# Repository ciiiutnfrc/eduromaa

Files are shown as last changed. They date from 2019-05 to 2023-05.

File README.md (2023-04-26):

# EduRoMAA - Robot Educativo Abierto y de Bajo Costo

El robot móvil EduRoMAA fue desarrollado con fines didácticos para la enseñanza de programación de sistemas embebidos utilizando la EduCIAA (versión educativa de la [Computadora Industrial Abierta Argentina](http://www.proyecto-ciaa.com.ar/)) en el [Centro de Investigación en Informática para la Ingeniería](http://ciii.frc.utn.edu.ar/PublicacionesCIII) de la [Universidad Tecnológica Nacional, Facultad Regional Córdoba](https://www.frc.utn.edu.ar/), bajo el proyecto [Robot móvil de hardware y software abierto con fines educativos en ingeniería electrónica](https://ciii.frc.utn.edu.ar/ciii/proyecto-utn4884/).

El robot EduRoMAA es un robot de tracción diferencial fabricado mediante corte láser e impresión 3D.
Dispone de dos ruedas de tracción controladas de forma independiente a fin de generar la trayectoria deseada, y una semiesfera que hace de apoyo.
Cuenta también con sensores de bajo costo comunes en robótica tales como: paragolpes, tacómetro en las ruedas, sensor de distancia por ultrasonido y sensores infrarrojos para la detección de línea; además de comunicación inalámbrica utilizando el protocolo Bluetooth.
El robot incluye las baterías de alimentación, el cargador por microUSB y fuente de tensión regulada.

El EduRoMAA cuenta con:
  * Tacómetros en las ruedas para la medición de velocidad.
  * Sensor de distancia por ultrasonido en la parte frontal.
  * Sensores de detección de líneas en la parte inferior.
  * Paragolpes en la parte trasera para detección de colisiones.
  * Comunicación inalámbrica por Bluetooth.
  * Bocina o buzzer.
  * Llave de encendido/apagado con LED indicador.
  * Baterías incorporadas con indicador de nivel y cargador por micro-USB.

Para la realización del EduRoMAA se utilizó únicamente software libre: [KiCAD](https://www.kicad.org/) para el circuito electrónico y PCB, [FreeCAD](https://www.freecadweb.org/) para la estructura mecánica y Eclipse IDE con GCC-ARM para el firmware.

## Videos

  * Despiece 3D de los componentes del EduRoMAA: [https://www.youtube.com/watch?v=gHjaK3ePBkI](https://www.youtube.com/watch?v=gHjaK3ePBkI).
  * Prueba de tracción del EduRoMAA: [https://www.youtube.com/watch?v=mks88KmrYdc](https://www.youtube.com/watch?v=mks88KmrYdc).

## Publicaciones
  * Gonzalo Perez-Paina, Martín Baudino, Diego Gonzalez-Dondo, Facundo Navarro, and Patricio Reus Merlo. **"Robot móvil de diseño abierto y bajo costo con fines didácticos basado en la educiaa"**. _In Proceedings of the X Jornadas Argentinas de Robótica (JAR)_. Neuquén, Argentina, 2019.

## Más información
  * [Características principales](doc/Caracteristicas.md).
  * Construcción:
    - Estructura mecánica.
    - Placa de acondicionamiento.
  * Ensamblado.
  * [Conexión con EduCIAA](doc/ConexionEduCIAA.md).
  * [Conexión con BluePill](doc/PlacaAdaptacionBluePill.md).
  * [Códigos de prueba para la versión EduCIAA](codigo/EduCIAA/)
  * [Códigos de prueba para la versión BluePill](codigo/BluePill/)

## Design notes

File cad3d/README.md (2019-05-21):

# Diseño en FreeCAD para corte láser

Archivos del diseño del robot utilizando [FreeCAD](https://www.freecadweb.org/). 
Se incluyen los archivos para realizar el corte láser en MDF (Medium Density Fibreboard) de 3mm de espesor.

## Los archivos son:

* EduRoMAATapas: diseño de la tapa inferior y superior.

* EduRoMAALaterales: diseño de los laterales izquierdo y derecho. 

* EduRoMAAFrente: diseño del frente donde se coloca el sensor de distancia por ultrasonido.

* EduRoMAAAtras: diseño de la parte trasera donde se sujeta el módulo Bluethoot

## Contenido de directorios

* **extra**: 
  * DibujoPCB: archivo de dibujo del contorno de la parte inferior del robot (exportado de FreeCAD para el diseño del PCB en KiCAD)
  * EsambleEstructura: archivo FreeCAD con el ensamble de la estructura del robot
* **pdf**: archivo pdf para el corte láser
* **svg**: archivos exportados desde FreeCAD para el corte láser

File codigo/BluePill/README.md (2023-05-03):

# Ejemplos de código en Arduino para la BluePill

En este directorio se ecuentran distintos ejemplos de código Arduino para testear los diferentes périfericos del EduRoMAA.

### Periféricos GPIOS: 
 * [Placa Adaptadora](testeoPlacaAdaptadora/testeoPlacaAdaptadora.ino): LEDs y Pulsadores de la placa
 * [Bocina](testeoBocina/testeoBocina.ino) 
 * [Paragolpes](testeoParagolpes/testeoParagolpes.ino)
 * [Sonar](testeoSonar/testeoSonar.ino)

### PWM
 * [Motores](testeoMotoresPWM/testeoMotoresPWM.ino) 

### Entrdas ADC:

* [Sensor seguidor de linea](testeoInfraRojo/testeoInfraRojo.ino)

### Entradas Timer

* [Encoder de las ruedas](testeoEncoders/testeoEncoders.ino)

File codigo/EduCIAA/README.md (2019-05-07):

* Buzzer: 
	- [x] Asignación de pines 
	- [x] Creación de header y source
	- [x] Codificación de módulo
	- [x] Implementación de test
	- [x] Test OK 

* Motores
	- [x] Asignación de pines 
	- [x] Creación de header y source
	- [x] Codificación de módulo
	- [x] Implementación de test
	- [ ] Test OK: Driver no funciona a 3.3V 

* Líneas Infrarrojos
	- [x] Asignación de pines 
	- [x] Creación de header y source
	- [x] Codificación de módulo
	- [x] Implementación de test
	- [ ] Test OK : Vref del ADC es 3.3 y señales salen con 0-5V

* Paragolpes
	- [x] Asignación de pines 
	- [x] Creación de header y source
	- [x] Codificación de módulo
	- [x] Implementación de test
	- [x] Test OK 

* Sonar
	- [x] Asignación de pines 
	- [x] Creación de header y source
	- [x] Codificación de módulo
	- [x] Implementación de test
	- [x] Test OK 

* Encoders IR
	- [x] Asignación de pines 
	- [x] Creación de header y source
	- [x] Codificación de módulo
	- [x] Implementación de test
	- [x] Test OK 

* Bluetooth
	- [x] Asignación de pines 
	- [ ] Creación de header y source
	- [ ] Codificación de módulo
	- [ ] Implementación de test
	- [ ] Test OK 
 
- [ ] 
- [ ] 
- [ ] 
- [ ] 
- [ ] 
- [ ]

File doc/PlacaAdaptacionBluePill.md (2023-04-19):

# Placa de adaptación para BluePill

Es un placa para adaptar el conexionado del EduRoMAA con la placa de desarrollo BluePill.

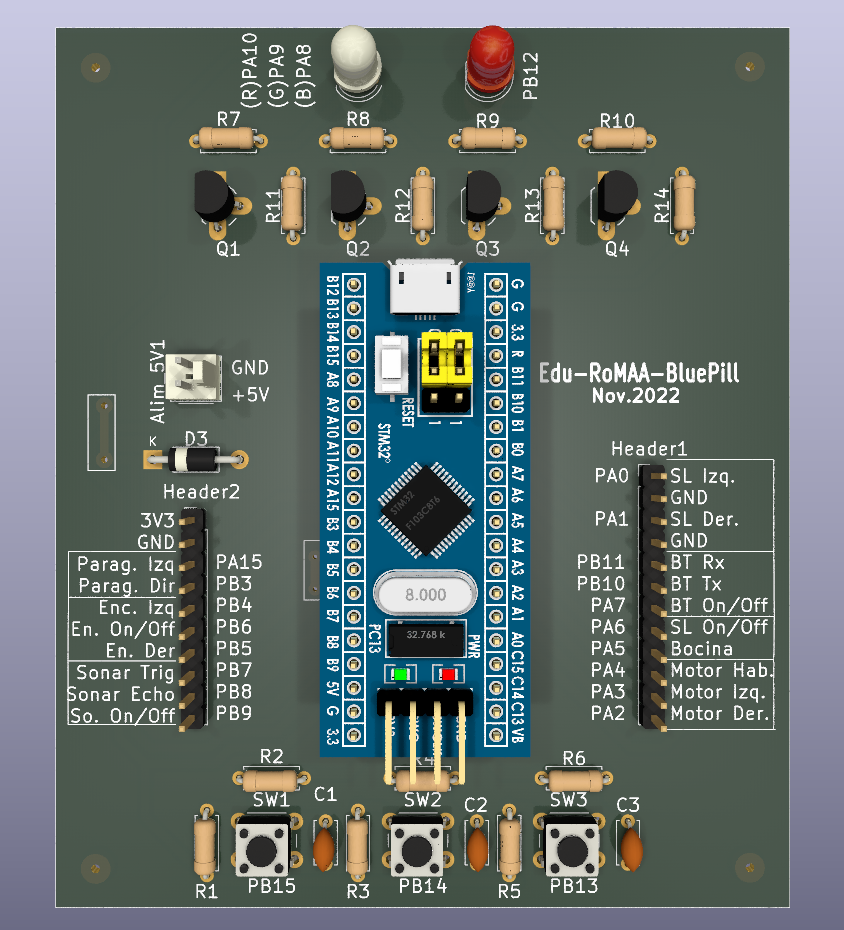
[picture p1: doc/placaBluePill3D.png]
a


## Características

* 3 pulsadores de propositos generales.

* 1 Led RGB.

* 1 Led rojo.

* 2 conectores para la utilización con el EduRoMAA.

* 1 conector para entrada de alimentación de 5V.

#### Asignación de pines de la BluePill

| Componente | Pin BluePill | Periferico |
| --- |:---:| --- |
| SW1 | PB15 | |
| SW2 | PB14 | |
| SW3 | PB13 | |
| LED RGB (Red) | PA10 | |
| LED RGB (Green) | PA9 | |
| LED RGB (Blue)  | PA8 | |
| LED Red | PB12 | |

##### Header 1 - conector con EduRoMAA

| Pin Conector | Componente EduRoMAA | Pin BluePill | |
|:---:| --- |:---:| --- |
| 1 | 3.3v | 3.3 | |
| 2 | GND | G | |
| 3 | Paragolpe Izquiero  | PA15 | |
| 4 | Paragolpe Derecho | PB3 | |
| 5 | Encoder Izquierdo | PB4 | |
| 6 | Enconder on/off | PB6 | |
| 7 | Encoder Derecho | PB5 | |
| 8 | Sonar Trigger | PB7 | |
| 9 | Sonar Echo | PB8 | |
| 10 | Sonar on/off | PB9 | |

##### Header 2 - conector con EduRoMAA

| Pin Conector | Componente | Pin BluePill | |
|:---:| --- |:---:| --- |
| 1 | Seguidor de Linea Izquierdo | PA0 | |
| 2 | GND | G | |
| 3 | Seguidor de Linea Derecho | PA1 | |
| 4 | GND | G | |
| 5 | BlueTooth Rx | PB11 | |
| 6 | BlueTooth Tx | PB10 | |
| 7 | BlueTooth on/off | PA7 | |
| 8 | Seguidor de Linea on/off | PA6 | |
| 9 | Bocina | PA5 | |
| 10 | Habilitación Motor | PA4 | |
| 11 | Motor Izquierdo | PA3 | |
| 12 | Motor Derecho | PA2 | |

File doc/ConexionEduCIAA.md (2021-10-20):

# Conexión con EduCIAA

En la siguiente tabla se muestra el conexionado de los componentes del robot con la placa EduCIAA.

|  # | Componentes | EduCIAA  | Pin | SCU Port_Pin | FUNC  |  Periférico |
|:--:|:---:|:---:|:---:|:---:|:-----:|:---:|
| 1  | Bocina | T_COL1 | 132 | P7_4 | FUNC0 | GPIO3[12] |
| 2  | Paragolpe izq. | CRS_DV | 64  | P1_16 | FUNC0 | GPIO0[3] |
| 3  | Paragolpe der. | RXD0 | 62  | P1_15 | FUNC0 | GPIO0[2] |
| 4  | Habilitación motores | T_FIL0 | 1 | P4_0 | FUNC0 | GPIO2[0] |
| 5  | PWM motor izq. | T_FIL3 | 7 | P4_3 | FUNC1 | CTOUT_3 |
| 6  | PWM motor der. | T_FIL2 | 8 | P4_2 | FUNC1 | CTOUT_0 |
| 7  | On/Off tacómetro | TXD0 | 67  | P1_18 | FUNC0 | GPIO0[13] |
| 8  | Tacómetro izq. | MDIO | 66  | P1_17 | FUNC4 | T0_CAP3 |
| 9  | Tacómetro der. | TXD1 | 70  | P1_20 | FUNC4 | T0_CAP2 |
| 10 | On/Off Detector línea  | CAN_TD | 116 | P3_2 | FUNC4 | GPIO5[9] |
| 11 | Detector línea izq. | CH2 | 143 | --- | --- | ADC0_2/ADC1_2 |
| 12 | Detector línea der. | CH1 | 2 | --- | --- | ADC0_1/ADC1_1 |
| 13 | On/Off Bluetooth | CAN_RD | 114 | P3_1 | FUNC4 | GPIO5[8] |
| 14 | Bluetooth Tx | RS232_TX | 87  | P2_3 | FUNC2 | U3_TXD |
| 15 | Bluetooth Rx | RS232_RX | 88  | P2_4 | FUNC2 | U3_RXD |
| 16 | On/Off sonar | GPIO4 | 86  | P6_8 | FUNC4 | GPIO5[16] |
| 17 | Sonar trigger | GPIO0 | 74  | P6_1 | FUNC0 | GPIO3[0] |
| 18 | Sonar echo | GPIO2 | 82  | P6_5 | FUNC0 | GPIO3[4] |

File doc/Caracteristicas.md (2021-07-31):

# Principales características

## Componentes

  * Motorreductor de corriente continua (6-9V) 48:1 (x2)
  * Sensor óptico TCST2103 (tacómetro) (x2)
  * Sensor reflectivo TCRT5000 (detección de línea) (x2)
  * Micro llave de detección de colisiones (paragolpes) (x2)
  * Sensor de distancia por ultrasonido HC-SR04 (sonar)
  * Módulo Bluetooth HC-05
  * Módulo cargador y fuente step-up (5V-2A)
  * Baterías de Li-Ion 18650 (2200mAh) (x2)

## Dimensiones

La siguiente figura muestra las cotas de la vista superior del robot.
<center>
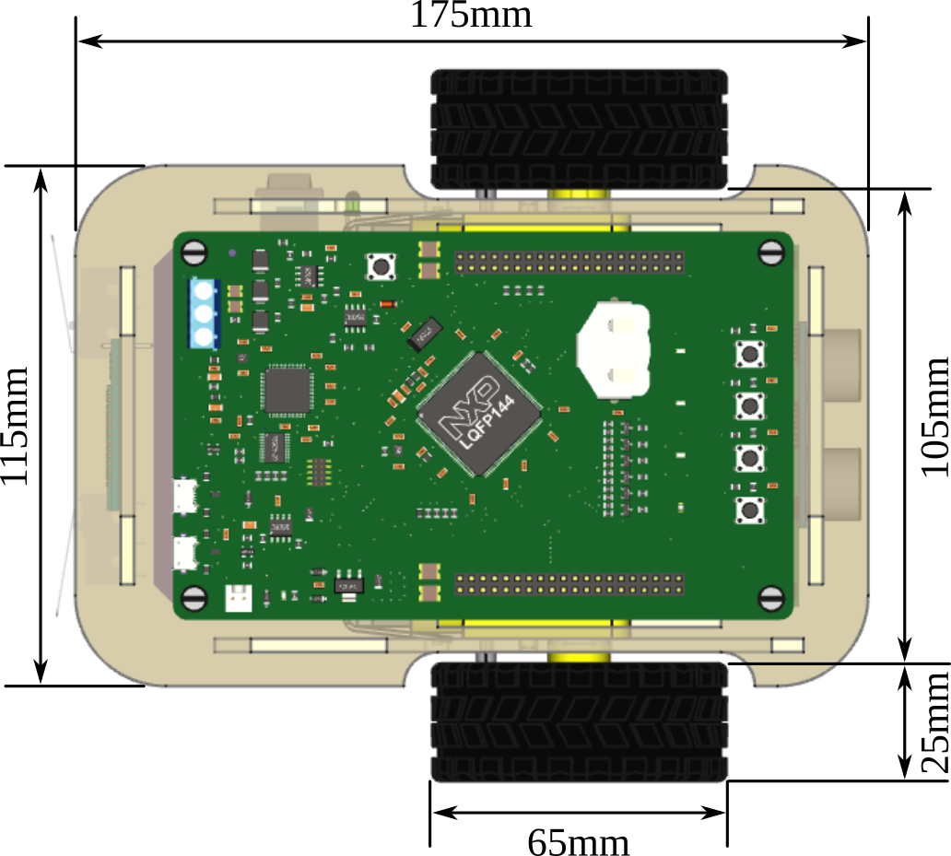
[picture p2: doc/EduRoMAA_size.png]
EduRoMAA size

</center>

La siguiente tabla muestra las dimensiones del robot.

| | |
|---|---|
| Dimensiones | Largo: 175 mm<br>Ancho: 115 mm<br>Altura: 55 mm |
| Diámetro de las ruedas | 65 mm |
| Distancia entre ruedas | 130 mm |
| Despeje del suelo | 10 mm |
| | |

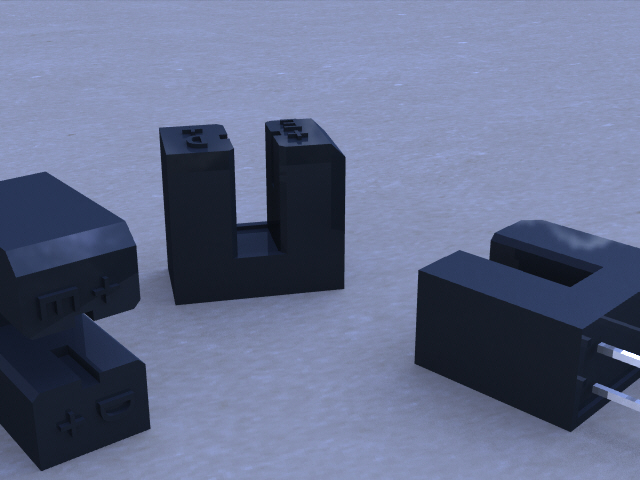
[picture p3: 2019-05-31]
placas/EduRoMAA-EduCIAA/3d_models/TCST1103/Renderings/TCST1103_2.jpg

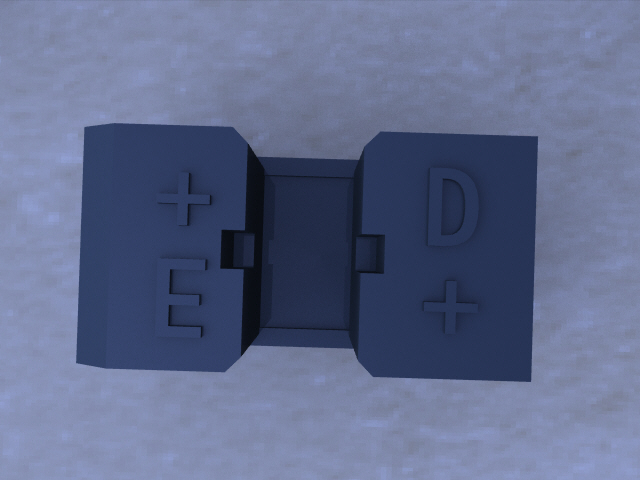
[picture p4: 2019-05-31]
placas/EduRoMAA-EduCIAA/3d_models/TCST1103/Renderings/TCST1103_1.jpg

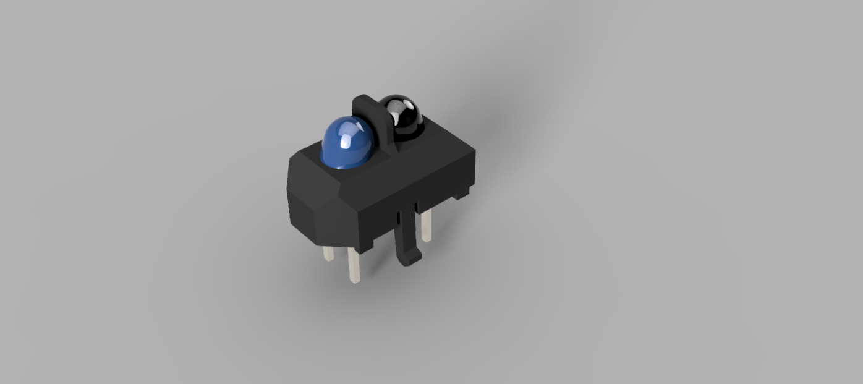
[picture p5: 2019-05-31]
placas/EduRoMAA-EduCIAA/3d_models/TCRT 5000/TCRT5000 .png

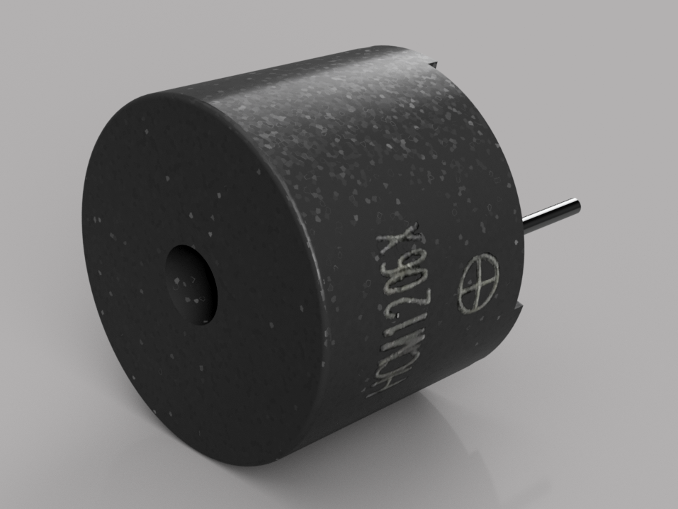
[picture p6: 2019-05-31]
placas/EduRoMAA-EduCIAA/3d_models/Buzzer/Buzzer_12mm/Renderings/Buzzer.png

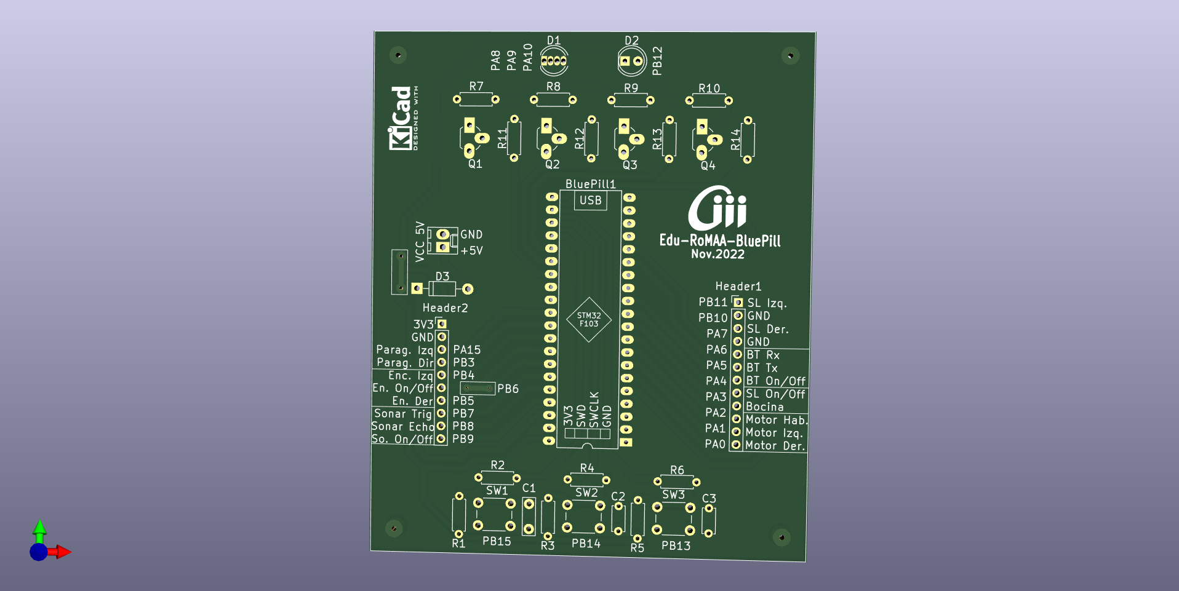
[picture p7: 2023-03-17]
placas/EduRoMAA-BluePill/BluePillAcond.png

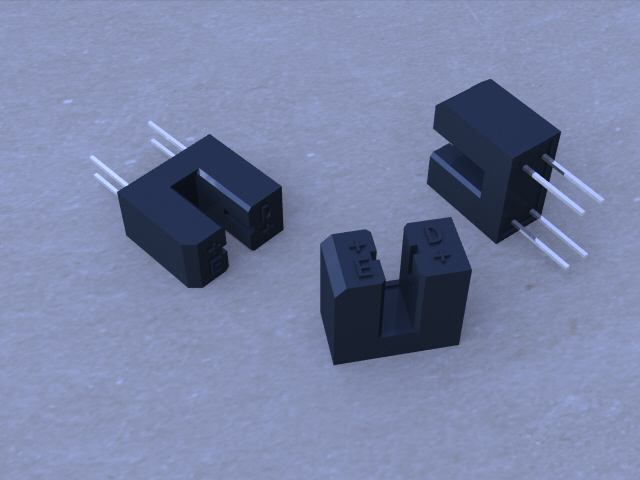
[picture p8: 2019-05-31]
placas/EduRoMAA-EduCIAA/3d_models/TCST1103/Renderings/TCST1103_0.jpg

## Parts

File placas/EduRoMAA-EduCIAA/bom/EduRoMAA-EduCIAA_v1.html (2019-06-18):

Source File | D:\Users\facun\Google Drive\Laboratorios\CIII\eduromaa\placas\EduRoMAA-EduCIAA\EduRoMAA-EduCIAA.sch
BoM Date | 18/6/2019 9:52:58 a. m.
Schematic Version | v00.00
Schematic Date | 2019-02-23
KiCad Version | Eeschema (5.1.0)-1
Component Groups | 29
Component Count (per PCB) | 77
Fitted Components (per PCB) | 77
Number of PCBs | 1
Total Component Count (for 1 PCBs) | 77
 | Description | Part | References | Value | Footprint | Quantity Per PCB | Datasheet
1 |  | Buzzer | BZ1 | Buzzer | Buzzer_12x9.5RM7.6 | 1
2 |  | C | C1 C2 C3 C5 C7 C8 C9 C10 C12 C13 | 0.1u | C_Disc_D6_P5 | 10
3 |  | CP1_Small | C14 | 100u | CP_Radial_D4.0mm_P2.00mm | 1 | ~
4 |  | CP1_Small | C4 C6 C11 | 10u | CP_Radial_D4.0mm_P2.00mm | 3 | ~
5 |  | Conn_01x10 | ConDer1 | Conn_01x10 | PinHeader_1x10_P2.54mm_Vertical | 1 | ~
6 |  | Conn_01x12 | ConIzq1 | Conn_01x12 | PinHeader_1x12_P2.54mm_Vertical | 1 | ~
7 |  | LED | D1 | LED | PinHeader_1x02_P2.54mm_Vertical | 1
8 |  | Conn_01x04 | J4 | Bluetooth | PinHeader_1x04_P2.54mm_Vertical | 1 | ~
9 |  | Conn_01x02 | J1 J7 | DC_IN | Molex_KK-254_AE-6410-02A_1x02_P2.54mm_Vertical | 2
10 |  | Conn_01x02 | J6 | DC_OUT | Molex_KK-254_AE-6410-02A_1x02_P2.54mm_Vertical | 1
11 |  | Conn_01x02 | J3 | Motor_Der | HDRV2W64P254_1X2_508X254X864 | 1
12 |  | Conn_01x02 | J2 | Motor_Izq | HDRV2W64P254_1X2_508X254X864 | 1
13 |  | Conn_01x04 | J5 | Sonar | PinSocket_1x04_P2.54mm_Vertical | 1 | ~
14 |  | Logo_CIII | Logo_1 | Logo_CIII | Logo_CIII_Small | 1
15 |  | Logo_CIII | Logo_2 | Logo_CIII | Logo_CIII_Small_FSilk | 1
16 |  | Logo_KiCad | Logo_4 | Logo_KiCad | KiCad-Logo2_8mm_SilkScreen | 1
17 |  | Logo_ohw | Logo_3 | Logo_ohw | OSHW-Logo_7.5x8mm_SilkScreen | 1
18 |  | BC548 | Q1 Q2 Q3 Q4 Q5 | BC548 | TO-92_mod | 5 | http://www.fairchildsemi.com/ds/BC/BC547.pdf
19 |  | R_US | R9 R10 R11 R13 R14 R15 R18 R19 R20 R21 R22 R25 R26 R27 R28 R29 R30 | 10k | Resistor_Horizontal_RM7mm | 17
20 |  | R_US | R4 R12 R17 R31 R32 R33 | 1k | Resistor_Horizontal_RM7mm | 6
21 |  | R_US | R1 R2 R3 R16 | 220 | Resistor_Horizontal_RM7mm | 4
22 |  | R_US | R7 R8 R23 R24 | 22k | Resistor_Horizontal_RM7mm | 4
23 |  | R_US | R5 R6 | 3.3k | Resistor_Horizontal_RM7mm | 2
24 |  | SW_Push | SW1 SW2 | SW_Push | HDRV2W64P254_1X2_508X254X864 | 2
25 |  | IRF7105 | U7 U8 | IRF7105 | SOIC-8_3.9x4.9mm_P1.27mm | 2
26 |  | L293D | U6 | L293D | DIP-16_W7.62mm_LongPads | 1
27 |  | LM393 | U4 | LM393 | DIP-8_W7.62mm_LongPads | 1
28 |  | TCRT5000 | U1 U2 | TCRT5000 | TCRT5000 | 2
29 |  | TCST1103 | U3 U5 | TCST1103 | TCST1103 | 2

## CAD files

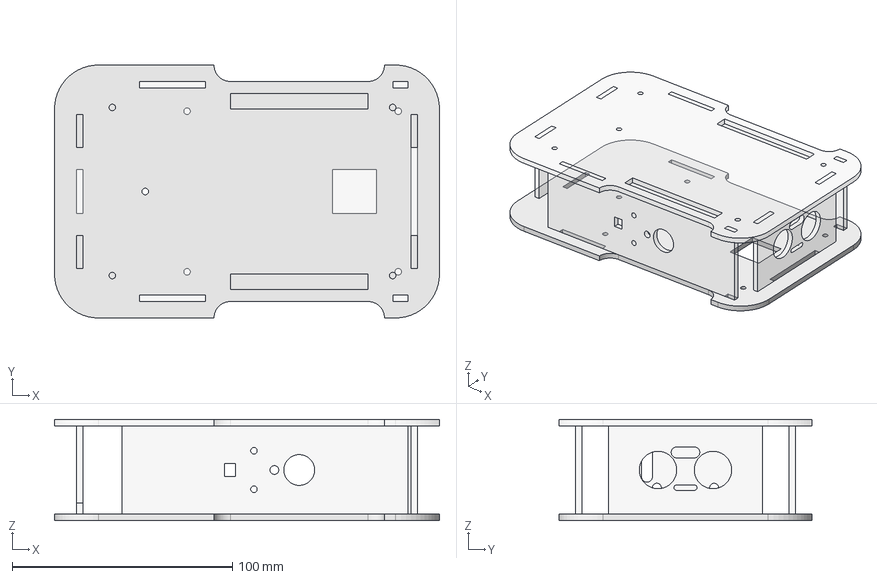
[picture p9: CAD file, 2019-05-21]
cad3d/extra/EsambleEstructura.fcstd
175.0 x 115.0 x 46.0 mm
TapaSuperior
LadoDerecho
LadoIzquierdo
Frente
Atras
TapaInferior

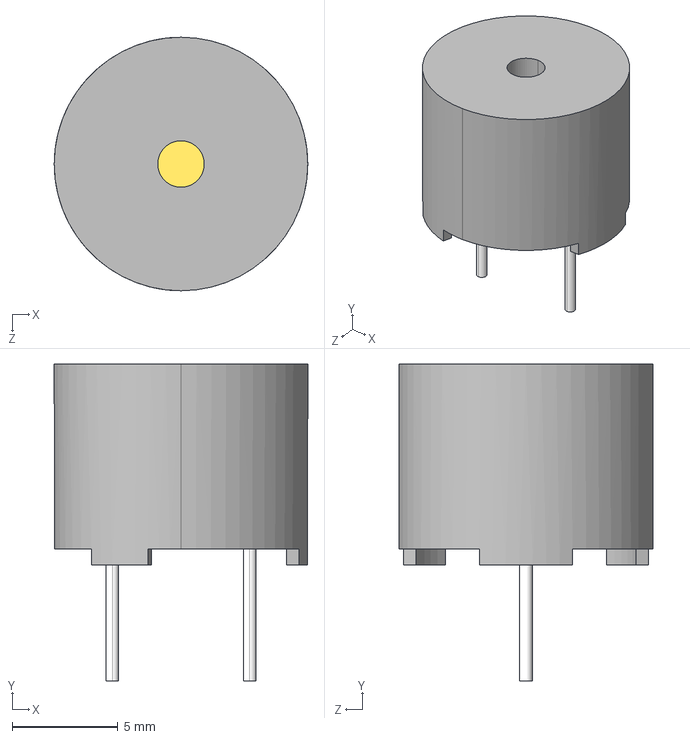
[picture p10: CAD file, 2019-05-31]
placas/EduRoMAA-EduCIAA/3d_models/Buzzer/Buzzer2.step
12.0 x 15.0 x 12.0 mm

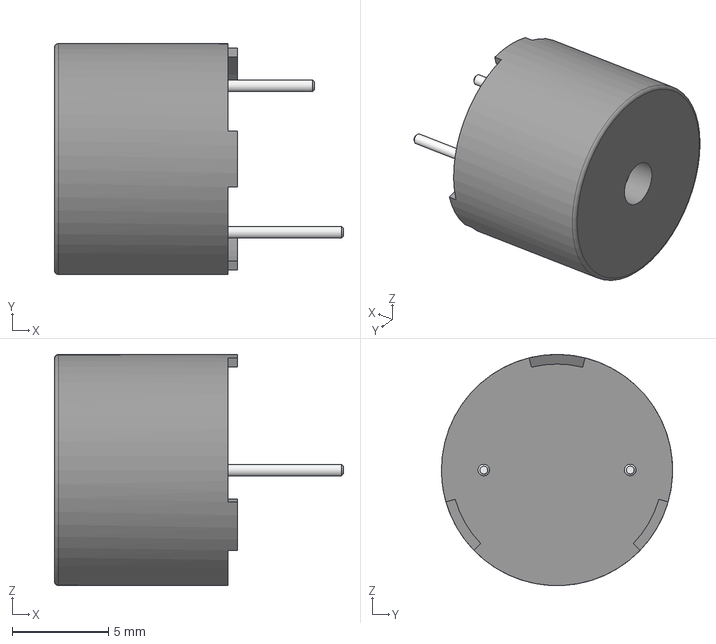
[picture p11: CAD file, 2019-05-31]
placas/EduRoMAA-EduCIAA/3d_models/Buzzer/Buzzer_12mm/Buzzer.step
15.0 x 12.0 x 12.0 mm

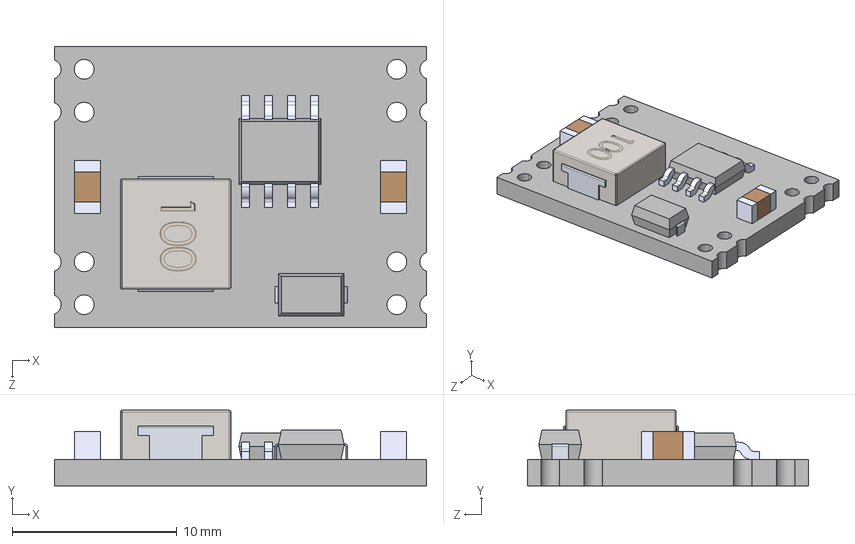
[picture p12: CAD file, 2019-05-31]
placas/EduRoMAA-EduCIAA/3d_models/MP1584_Buck/DC-DC_StepDown/DC-DC 5V-12V TO 3.3V STEP DOWN VOLTAGE REGULATOR POWER MODULE BOARD.STEP
22.6 x 4.60 x 17.1 mm
PCB, DC-DC 5V-12V TO 3.3V STEP DOWN VOLTAGE REGULATOR POWER MODULE BOARD
IC CHIP, DC-DC 5V-12V TO 3.3V STEP DOWN VOLTAGE REGULATOR POWER MODULE BOARD
INDUCTOR, DC-DC 5V-12V TO 3.3V STEP DOWN VOLTAGE REGULATOR POWER MODULE BOARD
SCHOTTKY DIODE, DC-DC 5V-12V TO 3.3V STEP DOWN VOLTAGE REGULATOR POWER MODULE BOARD
SMD RESISTOR, DC-DC 5V-12V TO 3.3V STEP DOWN VOLTAGE REGULATOR POWER MODULE BOARD x 2

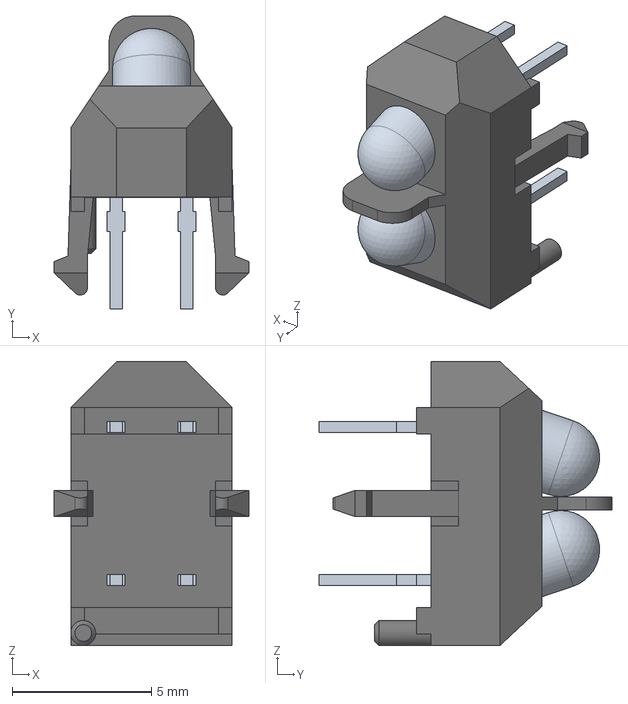
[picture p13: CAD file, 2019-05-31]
placas/EduRoMAA-EduCIAA/3d_models/TCRT 5000/TCRT5000.stp
7.00 x 10.5 x 10.2 mm
LEDs
Metal Contacts

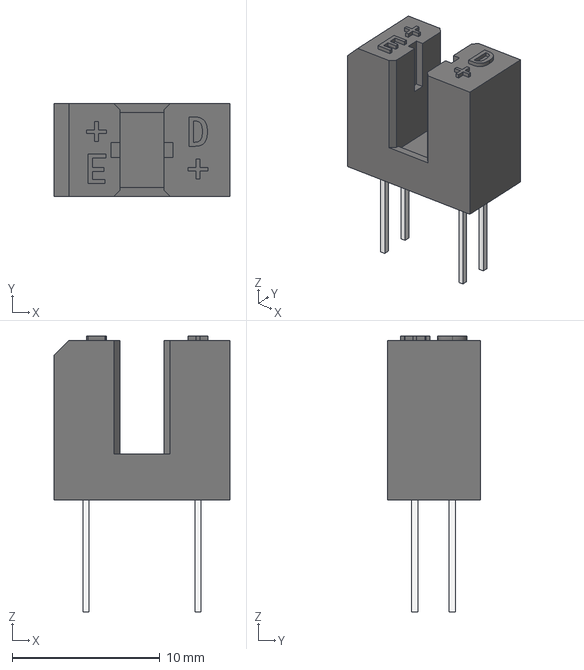
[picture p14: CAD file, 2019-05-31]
placas/EduRoMAA-EduCIAA/3d_models/TCST1103/TCST1103.stp
11.9 x 6.30 x 18.7 mm

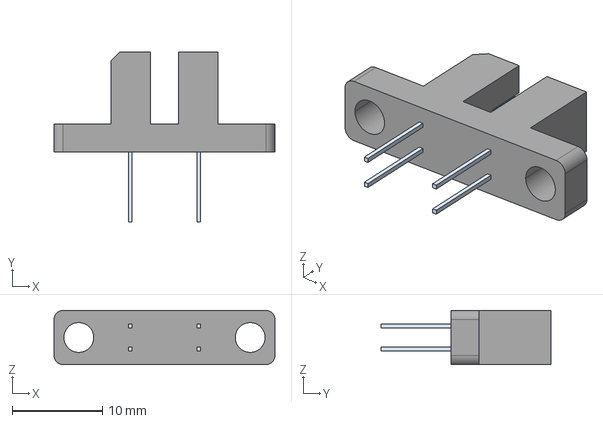
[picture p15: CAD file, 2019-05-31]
placas/EduRoMAA-EduCIAA/3d_models/TCST2103/tcst2202.stp
24.5 x 18.9 x 6.00 mm

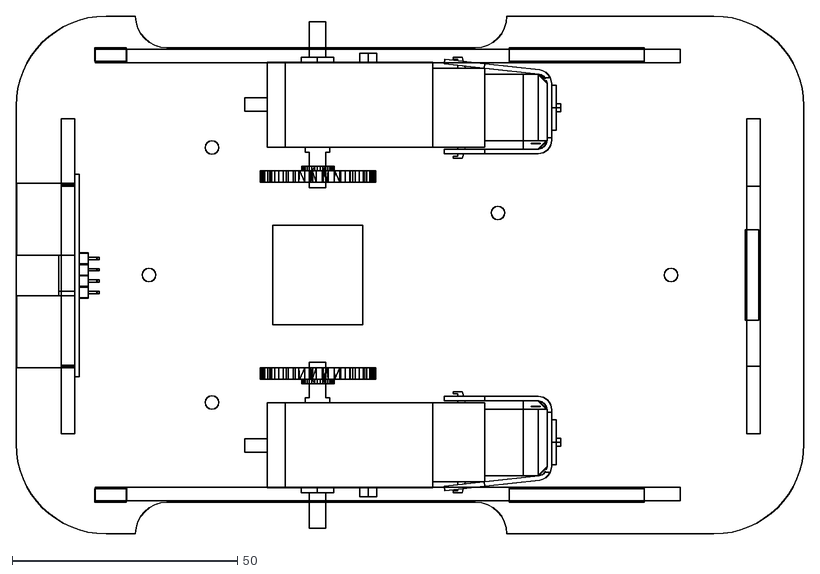
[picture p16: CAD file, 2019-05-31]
placas/EduRoMAA-EduCIAA/import/Base.dxf
175.0 x 115.0

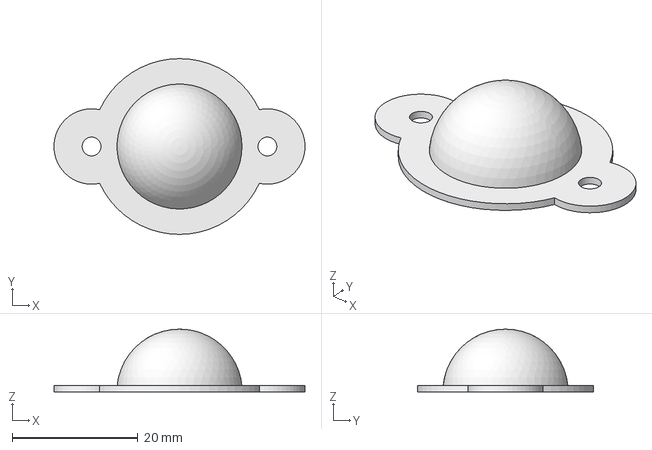
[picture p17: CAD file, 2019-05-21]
cad3d/EduRoMAACastor.fcstd
40.0 x 28.0 x 10.0 mm

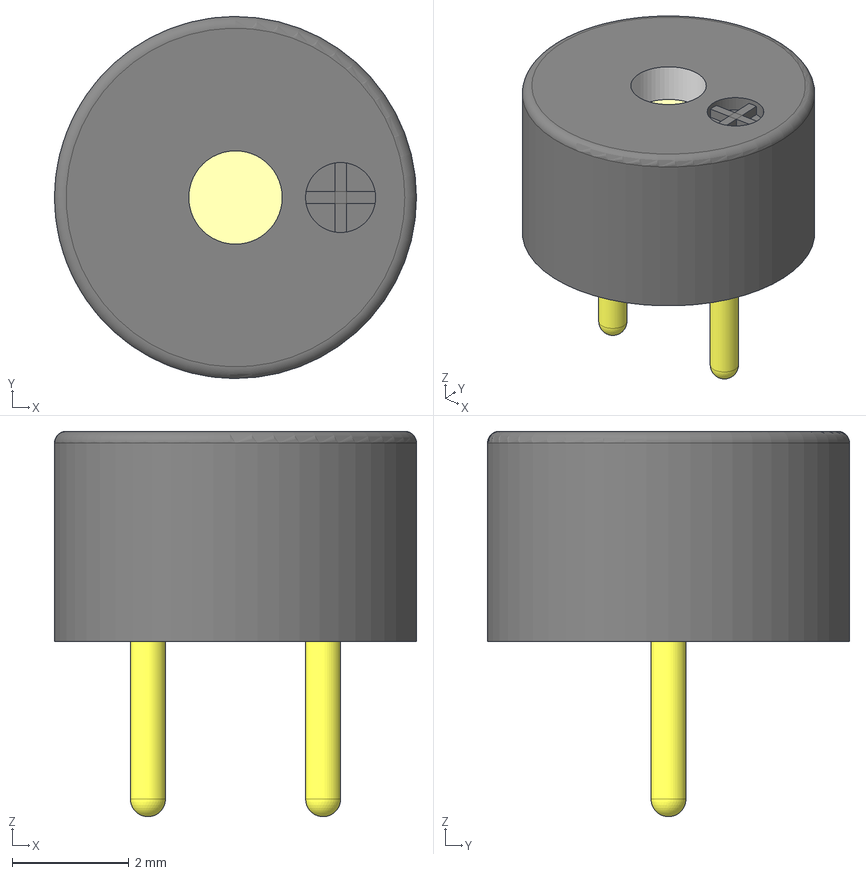
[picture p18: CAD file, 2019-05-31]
placas/EduRoMAA-EduCIAA/3d_models/Buzzer/Buzzer.stp
6.20 x 6.20 x 6.60 mm
Cilindro002
piu

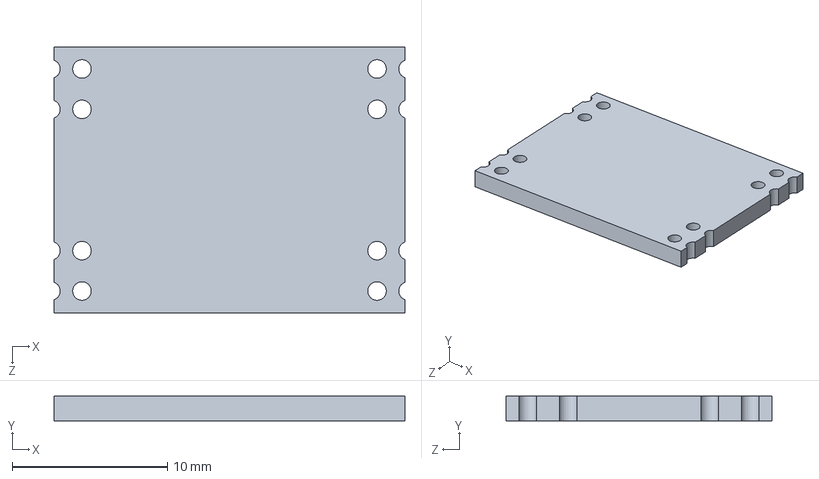
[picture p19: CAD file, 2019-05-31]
placas/EduRoMAA-EduCIAA/3d_models/MP1584_Buck/DC-DC_StepDown/PCB, DC-DC 5V-12V TO 3.3V STEP DOWN VOLTAGE REGULATOR POWER MODULE BOARD.SLDPRT
22.6 x 1.60 x 17.1 mm

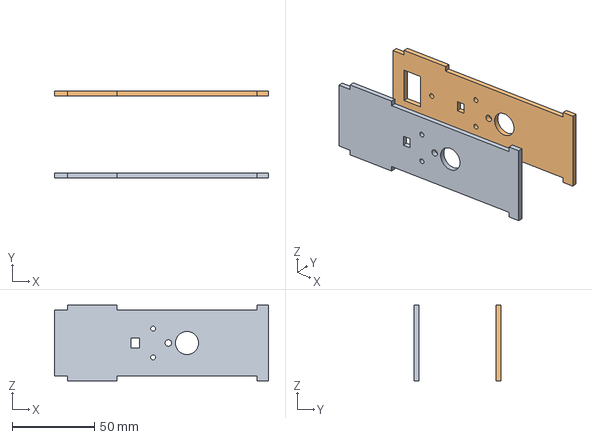
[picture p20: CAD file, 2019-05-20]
cad3d/EduRoMAALaterales.fcstd
130.0 x 53.0 x 46.0 mm
LadoDerechoMotor
LadoIzquierdoLlaveLED

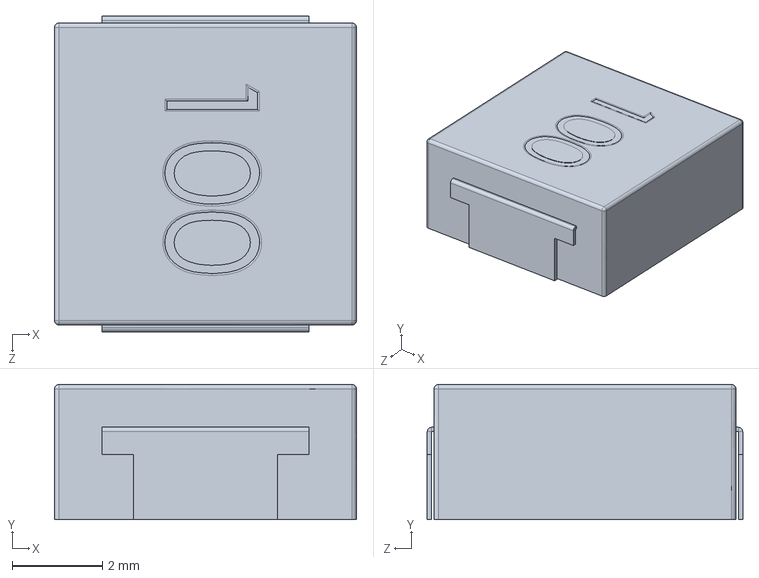
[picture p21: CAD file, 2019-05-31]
placas/EduRoMAA-EduCIAA/3d_models/MP1584_Buck/DC-DC_StepDown/INDUCTOR, DC-DC 5V-12V TO 3.3V STEP DOWN VOLTAGE REGULATOR POWER MODULE BOARD.SLDPRT
6.70 x 3.00 x 7.00 mm

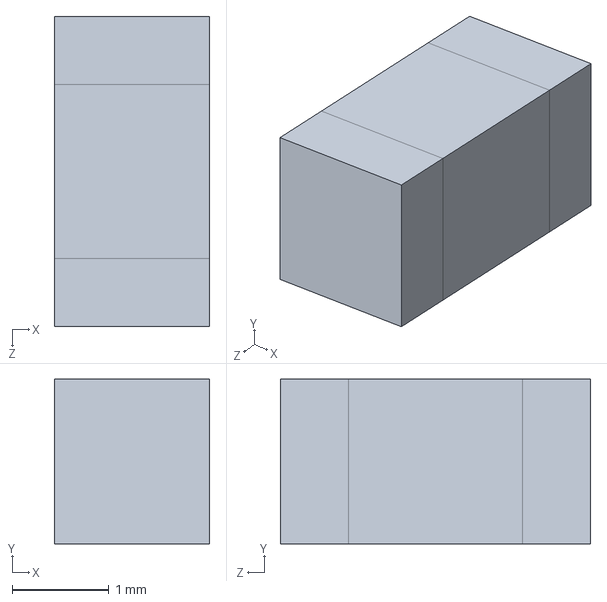
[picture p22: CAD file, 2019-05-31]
placas/EduRoMAA-EduCIAA/3d_models/MP1584_Buck/DC-DC_StepDown/SMD RESISTOR, DC-DC 5V-12V TO 3.3V STEP DOWN VOLTAGE REGULATOR POWER MODULE BOARD.SLDPRT
1.60 x 1.70 x 3.20 mm

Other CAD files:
cad3d/EduRoMAATapas.fcstd
placas/EduRoMAA-EduCIAA/3d_models/MP1584_Buck/MP1584_Buck.STEP
cad3d/extra/DibujoPCB.fcstd
cad3d/EduRoMAAFrente.fcstd
cad3d/EduRoMAAAtras.fcstd
cad3d/extra/DibujoPCB.dxf
cad3d/stl/EduRoMAACastor.stl
placas/EduRoMAA-EduCIAA/3d_models/Buzzer/Buzzer_12mm/Buzzer.iges
placas/EduRoMAA-EduCIAA/3d_models/MP1584_Buck/DC-DC_StepDown/DC-DC 5V-12V TO 3.3V STEP DOWN VOLTAGE REGULATOR POWER MODULE BOARD.SLDASM
placas/EduRoMAA-EduCIAA/3d_models/MP1584_Buck/DC-DC_StepDown/DC-DC 5V-12V TO 3.3V STEP DOWN VOLTAGE REGULATOR POWER MODULE BOARD.x_b
placas/EduRoMAA-EduCIAA/3d_models/MP1584_Buck/DC-DC_StepDown/IC CHIP, DC-DC 5V-12V TO 3.3V STEP DOWN VOLTAGE REGULATOR POWER MODULE BOARD.SLDPRT
placas/EduRoMAA-EduCIAA/3d_models/MP1584_Buck/DC-DC_StepDown/SCHOTTKY DIODE, DC-DC 5V-12V TO 3.3V STEP DOWN VOLTAGE REGULATOR POWER MODULE BOARD.SLDPRT
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

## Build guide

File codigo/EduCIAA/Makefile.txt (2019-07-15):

########################################################################
# Do not edit this file!!!
########################################################################
# -------- Program path and name default values ------------------------
# Program path
# relative to this folder, leave void if the program is in this folder
PROGRAM_PATH = examples/c
# Program name
PROGRAM_NAME = app
# -------- Program path and name from an external projec.mk file -------
-include program.mk

# Compose program path and name
ifeq ($(PROGRAM_PATH),)
PROGRAM_PATH_AND_NAME=$(PROGRAM_NAME)
else
PROGRAM_PATH_AND_NAME=$(PROGRAM_PATH)/$(PROGRAM_NAME)
endif

# -------- config.mk default values -----------------------------------
# Compile options
VERBOSE=n
OPT=g
USE_NANO=y
SEMIHOST=n
USE_FPU=y
# Libraries
USE_LPCOPEN=y
USE_SAPI=y
# -------- Include config.mk file fom program --------------------------
-include $(PROGRAM_PATH_AND_NAME)/config.mk
# ----------------------------------------------------------------------

MODULES=$(sort $(dir $(wildcard libs/*/)))
SRC=$(wildcard $(PROGRAM_PATH_AND_NAME)/src/*.c)
SRC+=$(foreach m, $(MODULES), $(wildcard $(m)/src/*.c))

# 20190709 - MSB - Agragada librería de EduRoMAA
INCLUDES += -Ieduromaa/lib/inc
SRC+=$(wildcard eduromaa/lib/src/*.c)

CXXSRC=$(wildcard $(PROGRAM_PATH_AND_NAME)/src/*.cpp)
CXXSRC+=$(foreach m, $(MODULES), $(wildcard $(m)/src/*.cpp))

ASRC=$(wildcard $(PROGRAM_PATH_AND_NAME)/src/*.s)
ASRC+=$(foreach m, $(MODULES), $(wildcard $(m)/src/*.s))

OUT=$(PROGRAM_PATH_AND_NAME)/out
OBJECTS=$(CXXSRC:%.cpp=$(OUT)/%.o) $(ASRC:%.s=$(OUT)/%.o) $(SRC:%.c=$(OUT)/%.o)
DEPS=$(OBJECTS:%.o=%.d)

# 20190609 - MSB - Modificado de lpc4337.cfg para compatibilizar con OpenOCD v0.10
OOCD_SCRIPT=scripts/openocd/lpc4337_v10.cfg

TARGET=$(OUT)/$(PROGRAM_NAME).elf
TARGET_BIN=$(basename $(TARGET)).bin
TARGET_LST=$(basename $(TARGET)).lst
TARGET_MAP=$(basename $(TARGET)).map
TARGET_NM=$(basename $(TARGET)).names.csv

INCLUDE_FLAGS=$(foreach m, $(MODULES), -I$(m)/inc) -I$(PROGRAM_PATH_AND_NAME)/inc $(INCLUDES)
DEFINES_FLAGS=$(foreach m, $(DEFINES), -D$(m))
OPT_FLAGS=-ggdb3 -O$(OPT) -ffunction-sections -fdata-sections
LIBSDEPS=$(addprefix $(OUT)/, $(addsuffix .a, $(basename $(foreach l, $(LIBS), $(foreach m, $(MODULES), $(wildcard $(m)/lib/lib$(l).hexlib) ) ))))

COMMON_FLAGS=$(ARCH_FLAGS) $(DEFINES_FLAGS) $(INCLUDE_FLAGS) $(OPT_FLAGS)

CFLAGS=$(COMMON_FLAGS) -std=c99
CXXFLAGS=$(COMMON_FLAGS) -fno-rtti -fno-exceptions -std=c++11

LDFLAGS=$(ARCH_FLAGS)
LDFLAGS+=$(addprefix -L, $(foreach m, $(MODULES), $(wildcard $(m)/lib)))
LDFLAGS+=$(addprefix -L, $(wildcard $(dir $(LIBSDEPS))))
LDFLAGS+=$(addprefix -l, $(LIBS))
LDFLAGS+=-T$(LDSCRIPT)
LDFLAGS+=-nostartfiles -Wl,-gc-sections -Wl,-Map=$(TARGET_MAP) -Wl,--cref

ifeq ($(USE_NANO),y)
LDFLAGS+=--specs=nano.specs
endif

ifeq ($(SEMIHOST),y)
DEFINES+=USE_SEMIHOST
LDFLAGS+=--specs=rdimon.specs
endif

CROSS=arm-none-eabi-
CC=$(CROSS)gcc
CXX=$(CROSS)g++
ifeq ($(CXXSRC),)
LD=$(CROSS)gcc
else
LD=$(CROSS)g++
endif
SIZE=$(CROSS)size
LIST=$(CROSS)objdump -xdS
OBJCOPY=$(CROSS)objcopy
NM=$(CROSS)nm
GDB=$(CROSS)gdb
OOCD=openocd

ifeq ($(VERBOSE),y)
Q=
else
Q=@
endif

# Build program

all: $(TARGET) $(TARGET_BIN) $(TARGET_LST) $(TARGET_NM) size

-include $(foreach m, $(MODULES), $(wildcard $(m)/module.mk))

-include $(DEPS)

$(OUT)/%.o: %.c
	@echo CC $(notdir $<)
	@mkdir -p $(dir $@)
	$(Q)$(CC) -MMD $(CFLAGS) -c -o $@ $<

$(OUT)/%.o: %.cpp
	@echo CXX $(notdir $<)
	@mkdir -p $(dir $@)
	$(Q)$(CXX) -MMD $(CXXFLAGS) -c -o $@ $<

$(OUT)/%.o: %.s
	@echo AS $(notdir $<)
	@mkdir -p $(dir $@)
	$(Q)$(CC) -MMD $(CFLAGS) -c -o $@ $<

$(OUT)/%.a: %.hexlib
	@echo DEBLOB $(notdir $<)
	@mkdir -p $(dir $@)
	$(Q)$(OBJCOPY) -I ihex -O binary $< $@

$(OUT)/linker-params: $(OBJECTS) $(LIBSDEPS) Makefile
	@echo LD params
	@mkdir -p $(dir $@)
	$(Q)echo "-Wl,-( $(OBJECTS) -Wl,-) $(LDFLAGS)" > $@

$(TARGET): $(OUT)/linker-params
	@echo LD $@...
	$(Q)$(LD) -o $@ @$(OUT)/linker-params

$(TARGET_BIN): $(TARGET)
	@echo COPY $(notdir $<) TO $(notdir $@)
	@mkdir -p $(dir $@)
	$(Q)$(OBJCOPY) -O binary $< $@

$(TARGET_LST): $(TARGET)
	@echo LIST
	$(Q)$(LIST) $< > $@

# If you have sed
#$(TARGET_NM): $(TARGET)
#	@echo NAME
#	$(Q)$(NM) -nAsSCp $< \
#		| sed -r 's/(.+?\:[^ ]+) ([a-zA-Z\?] [a-zA-Z_].*)/\1 00000000 \2/' \
#		| sed -r 's/(.+?)\:([a-fA-F0-9]+) ([a-fA-F0-9]+) ([a-zA-Z\?]) (.*)/\1\t0x\2\t0x\3\t\4\t\5/' \
#		> $@

# If you doesn't have sed
$(TARGET_NM): $(TARGET)
	@echo NAME
	$(Q)$(NM) -nAsSCp $< > $@

# Build program size

size: $(TARGET)
	$(Q)$(SIZE) $<

# Download a program into board
# Eliminada la opci�n "unlock" que traba write_image en OpenOCD v0.10 
.download_flash: $(TARGET_BIN)
	@echo DOWNLOAD to FLASH
	$(Q)$(OOCD) -f $(OOCD_SCRIPT) \
		-c "init" \
		-c "halt 0" \
		-c "flash write_image erase $< 0x1A000000 bin" \
		-c "reset run" \
		-c "shutdown" 2>&1

.download_ram: $(TARGET_BIN)
	@echo DOWNLOAD to RAM
	$(Q)$(OOCD) -f $(OOCD_SCRIPT) \
			 -c "init" \
			 -c "halt 0" \
			 -c "load_image $< 0x20000000 bin" \
			 -c "reset run" \
			 -c "shutdown" 2>&1

ifeq ($(LOAD_INRAM),y)
download: .download_ram
else
download: .download_flash
endif

# Erase Flash memory

erase:
	@echo ERASE
	$(Q)$(OOCD) -f $(OOCD_SCRIPT) \
		-c "init" \
		-c "halt 0" \
		-c "flash erase_sector 0 0 last" \
		-c "shutdown" 2>&1

# Remove compilation generated files

clean:
	@echo CLEAN
	$(Q)rm -fR $(OBJECTS) $(TARGET) $(TARGET_BIN) $(TARGET_LST) $(DEPS) $(OUT)

clean_all:
	@echo CLEAN ALL
	@sh scripts/program/clean_all.sh

# Debug with Embedded IDE

.debug:
	@echo DEBUG
	$(Q)$(OOCD) -f $(OOCD_SCRIPT) 2>&1

.run: $(TARGET)
	$(Q)$(OOCD) -f $(OOCD_SCRIPT) &
	$(Q)socketwaiter :3333 && arm-none-eabi-gdb -batch $(TARGET) -x scripts/openocd/gdbinit

# Information

.info:
	LANG=C $(MAKE) -B -p  -r -n

# Tests

# Build all programs
.test_build_all:
	@sh scripts/test/test-build-all.sh

# Run Hardware tests
.hardware_test: $(TARGET)
	$(Q)$(OOCD) -f $(OOCD_SCRIPT) > $(TARGET).log &
	$(Q)sleep 3 && arm-none-eabi-gdb -batch $(TARGET) -x scripts/openocd/gdbinit
	$(Q)cat $(TARGET).log
	$(Q)cat $(TARGET).log | grep FAIL -o >/dev/null && exit 1 || exit 0

# New program generator
new_program:
	@sh scripts/program/new_program.sh

# Select program to compile
select_program:
	@sh scripts/program/select_program.sh

.PHONY: all size download erase clean new_program select_program

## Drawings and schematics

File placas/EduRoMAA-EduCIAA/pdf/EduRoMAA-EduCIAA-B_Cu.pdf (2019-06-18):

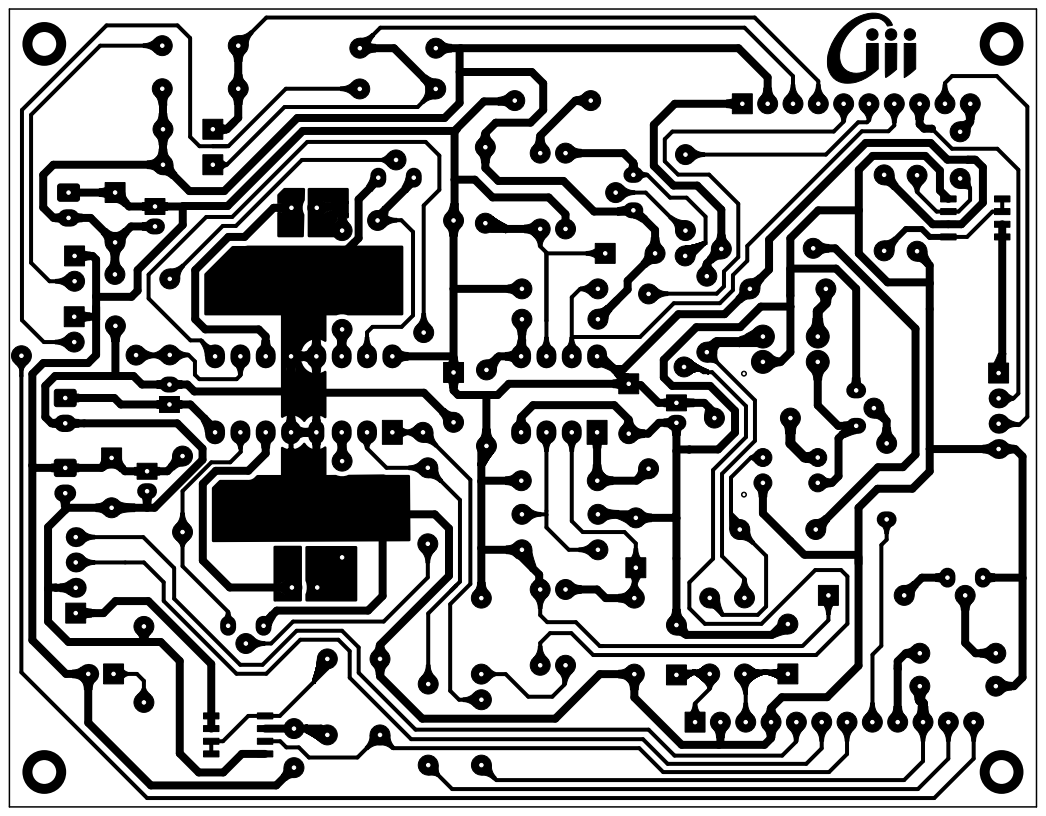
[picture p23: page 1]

File: EduRoMAA-EduCIAA.kicad_pcb Sheet:
Id: 1/1 Title:

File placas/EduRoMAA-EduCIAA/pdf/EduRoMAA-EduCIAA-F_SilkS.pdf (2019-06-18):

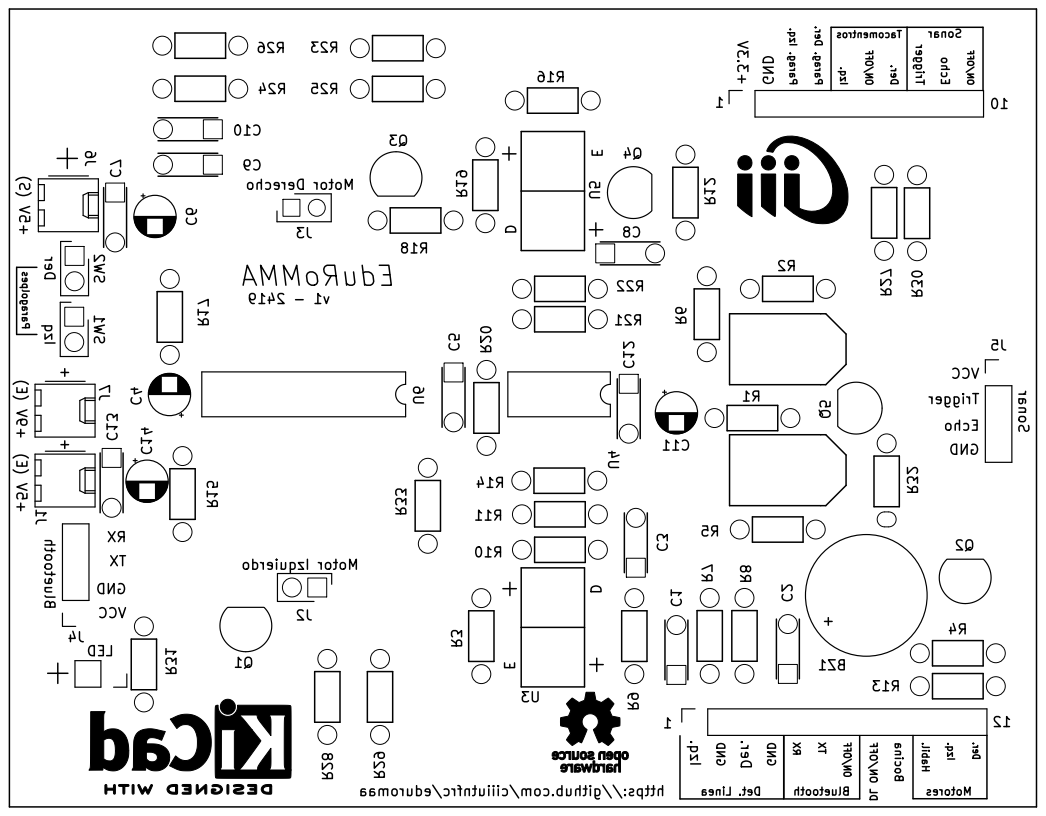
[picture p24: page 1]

Tacomentros Sonar +3.3V GND Parag. Izq. Parag. Der. Izq. ON/OFF Der. Trigger Echo ON/OFF 1 12 1 10 ParagolpesDer Izq +5V (E) +9V (E) +5V (S) Sonar GND

TXGND Motor Izquierdo Motor Derecho

File: EduRoMAA-EduCIAA.kicad_pcb Sheet: EduRoMMA

v1 - 2419 LED Izq. Der. Motores Habil. Bocina Bluetooth DL ON/OFFTX ON/OFF RX Det. Linea Izq. GND Der. GND

https://github.com/ciiiutnfrc/eduromaa

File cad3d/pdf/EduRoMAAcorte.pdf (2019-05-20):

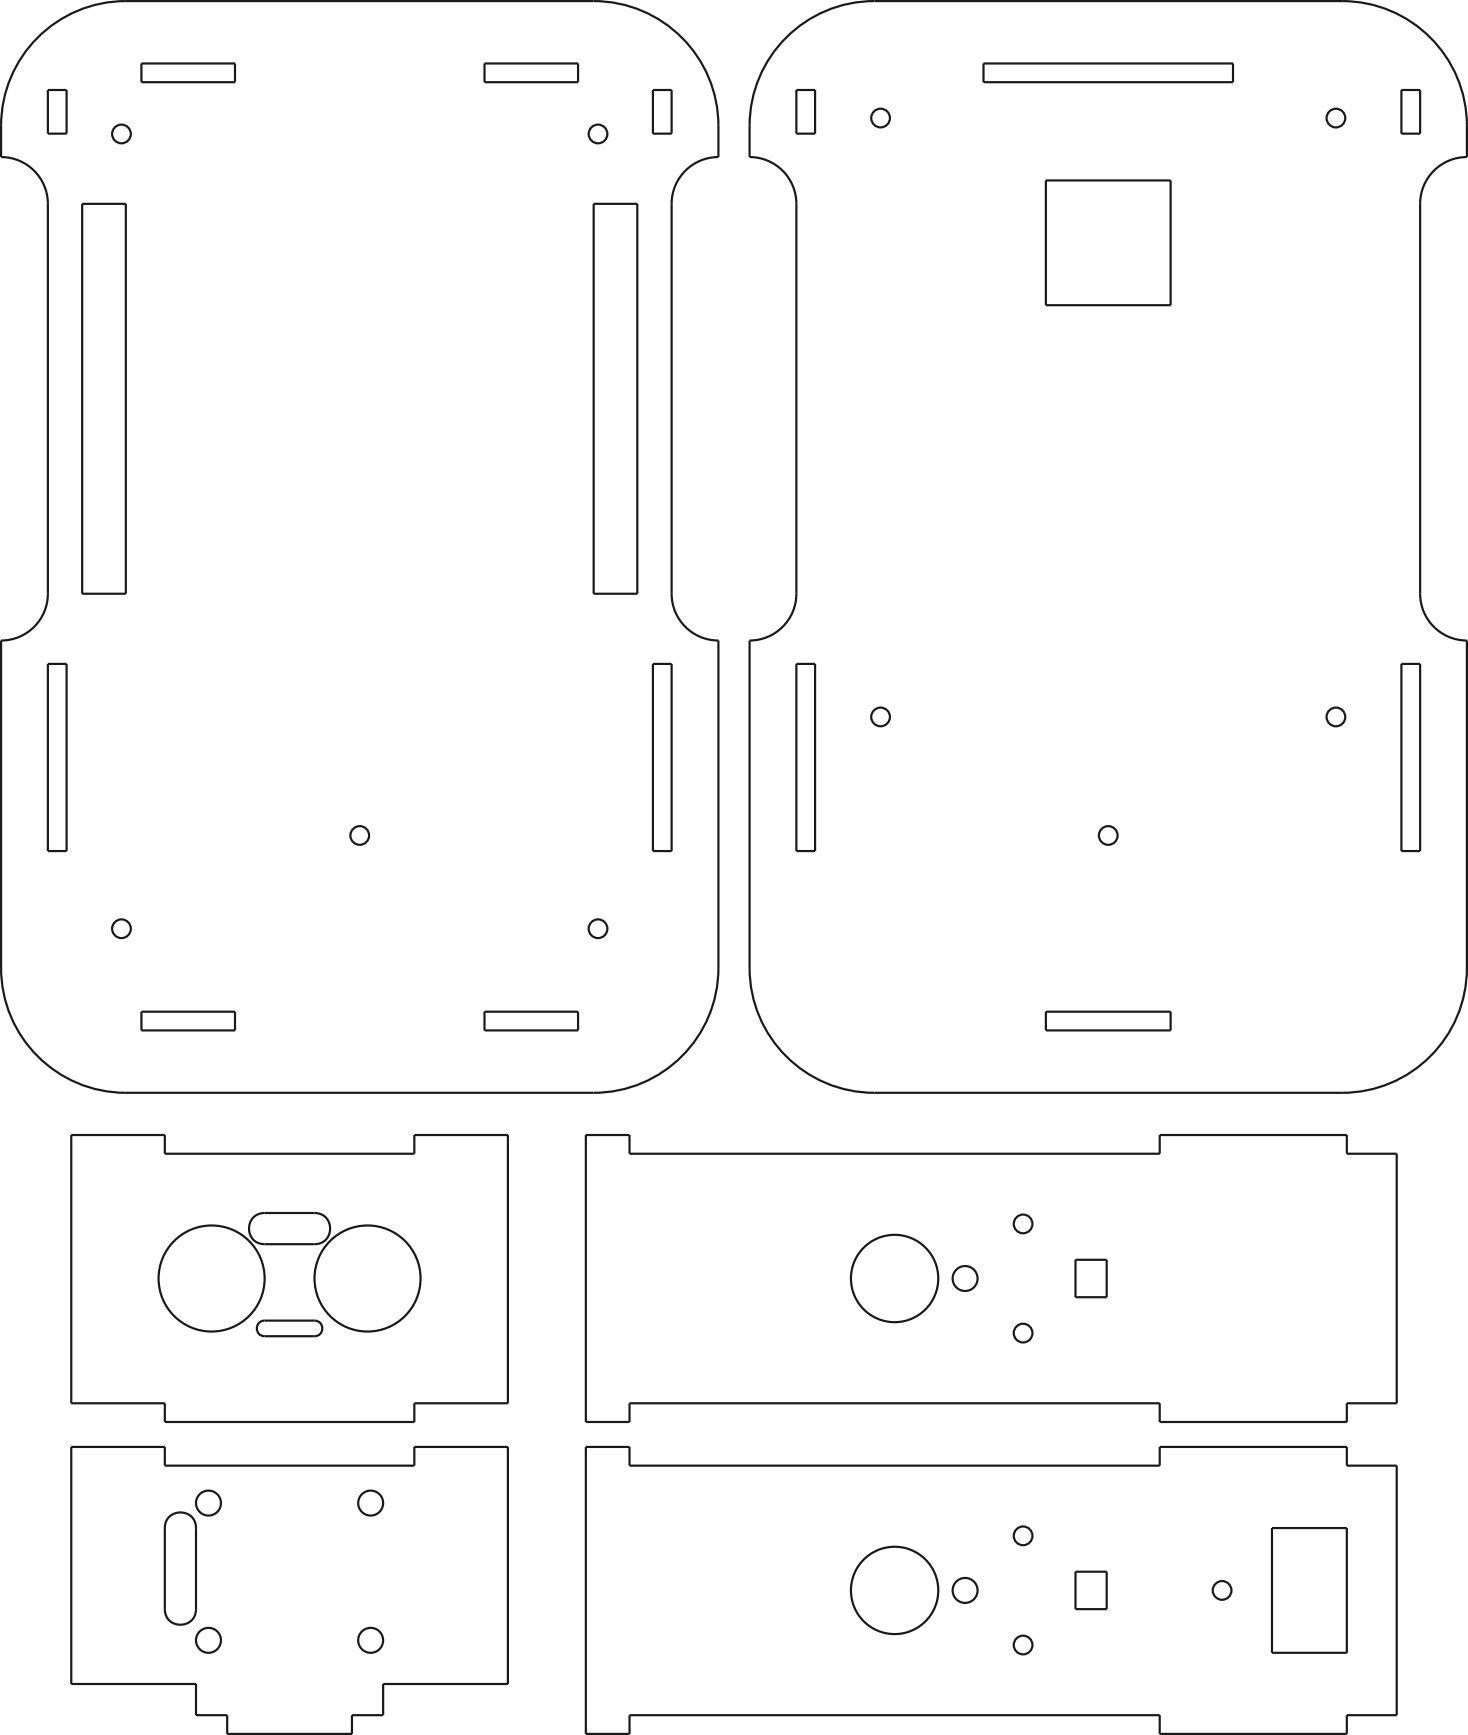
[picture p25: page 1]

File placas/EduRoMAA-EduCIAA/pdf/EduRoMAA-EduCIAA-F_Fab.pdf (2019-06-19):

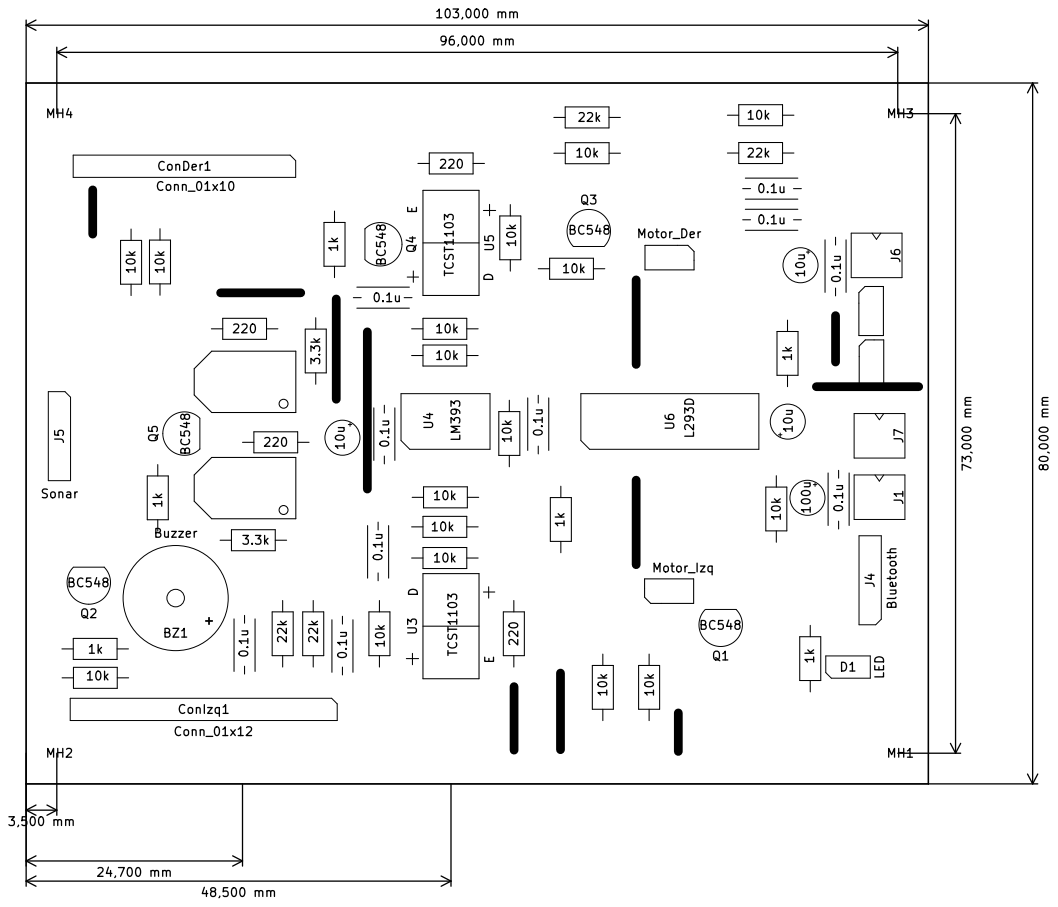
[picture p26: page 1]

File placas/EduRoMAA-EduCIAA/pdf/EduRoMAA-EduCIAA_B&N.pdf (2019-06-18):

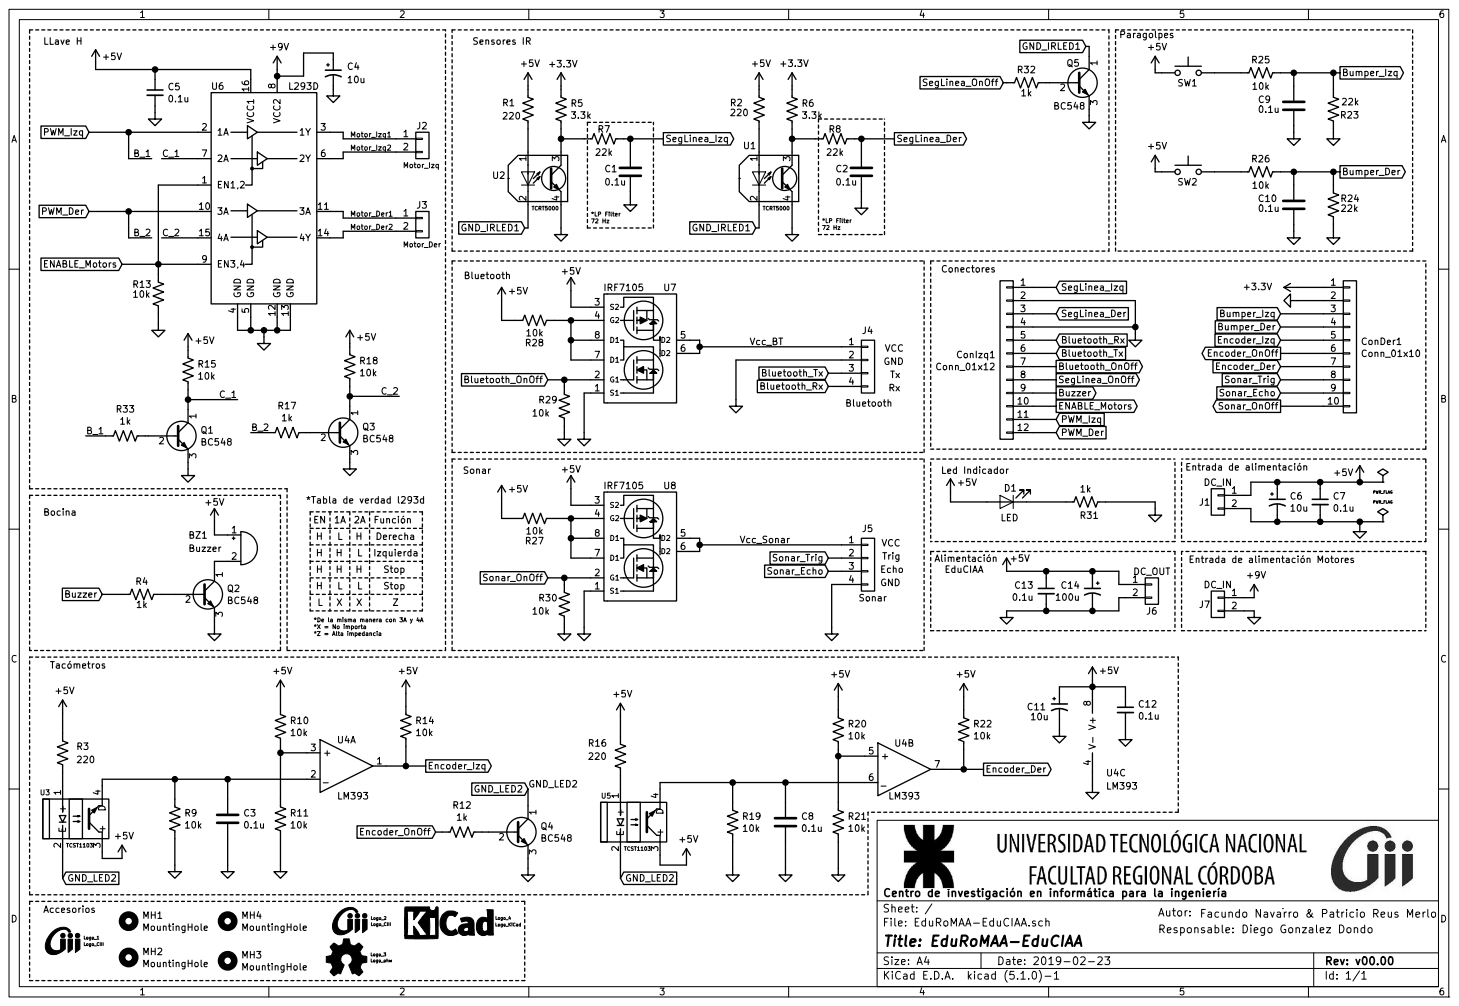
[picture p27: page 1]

*De la misma manera con 3A y 4A
*X = No importa
*Z = Alta impedancia

Id: 1/1 Title: EduRoMAA-EduCIAA

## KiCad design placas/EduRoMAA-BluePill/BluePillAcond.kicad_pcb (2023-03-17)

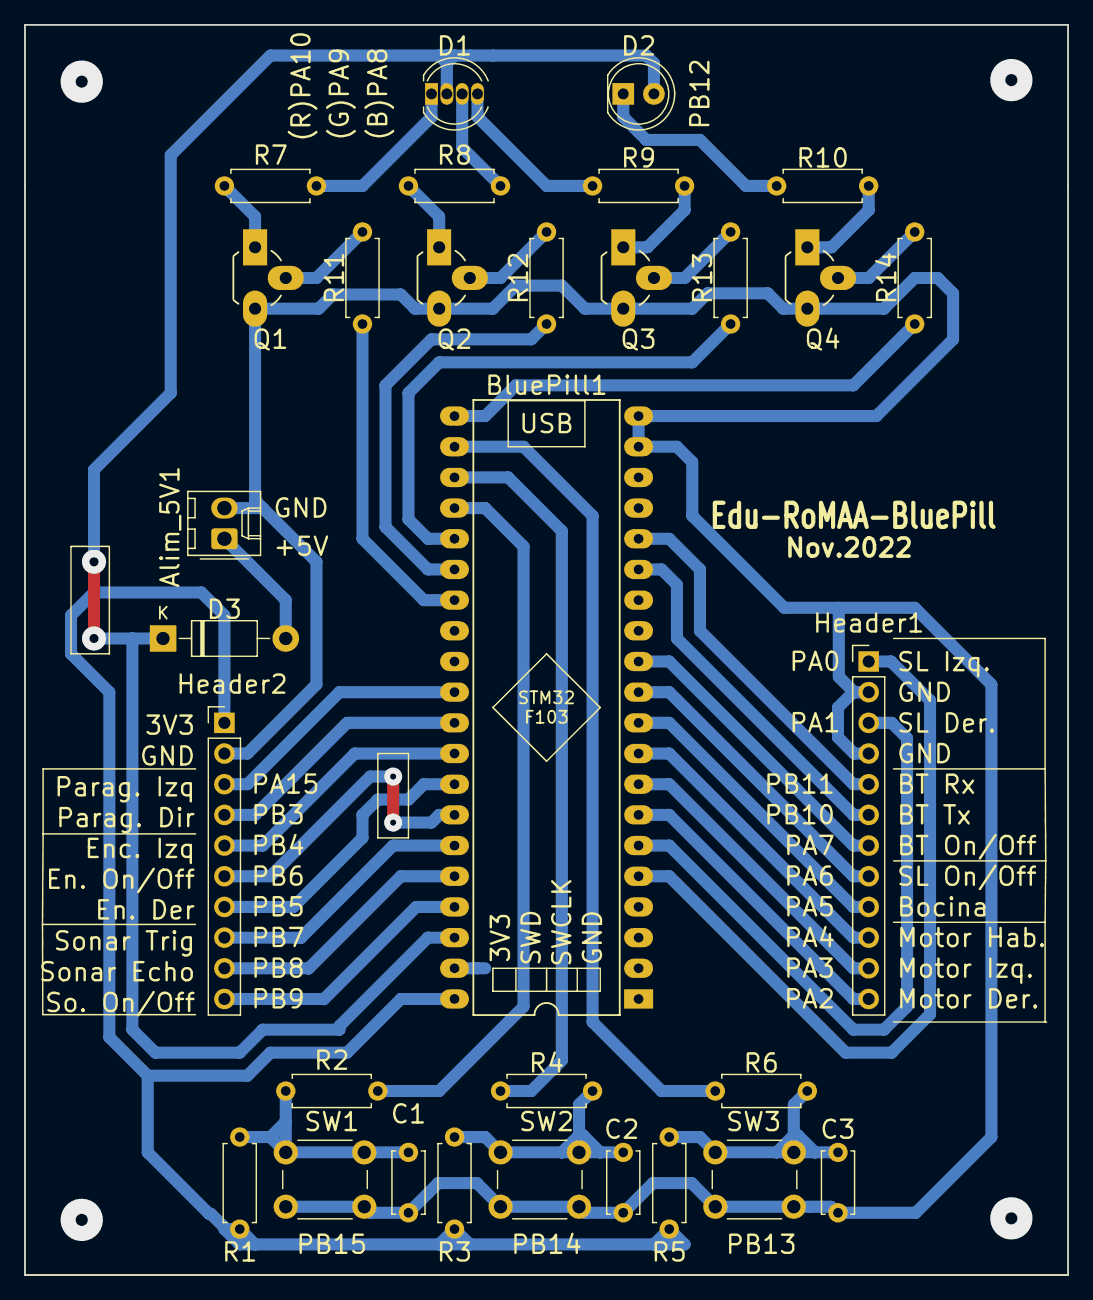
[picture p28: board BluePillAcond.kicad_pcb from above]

Board: 2 copper layers, 86.4 x 103.5 mm, 31 parts (0 on the bottom side), 44 nets.

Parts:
Alim_5V1: Conn_01x02; Molex_KK-254_AE-6410-02A_1x02_P2.54mm_Vertical
BluePill1: Conn_02x20_Counter_Clockwise; DIP-40_W15.24mm_LongPads
C1, C2, C3: 100nF; C_Disc_D5.0mm_W2.5mm_P5.00mm
D1: LED_RGBA; LED_D5.0mm-4_RGB
D2: LED Rojo; LED_D5.0mm
D3: 1N4007; D_DO-41_SOD81_P10.16mm_Horizontal
Header1: Conn_01x12; PinHeader_1x12_P2.54mm_Vertical
Header2: Conn_01x10; PinHeader_1x10_P2.54mm_Vertical
Q1, Q2, Q3, Q4: BC548; TO-92_Rugged
R1, R3, R5: 10k; R_Axial_DIN0207_L6.3mm_D2.5mm_P7.62mm_Horizontal
R2, R4, R6: 1k; R_Axial_DIN0207_L6.3mm_D2.5mm_P7.62mm_Horizontal
R7, R8, R9, R10: 220; R_Axial_DIN0207_L6.3mm_D2.5mm_P7.62mm_Horizontal
R11, R12, R13, R14: 2k2; R_Axial_DIN0207_L6.3mm_D2.5mm_P7.62mm_Horizontal
SW1, SW2, SW3: SW_Push; SW_PUSH_6mm_H4.3mm

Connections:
5V: BluePill1.38, D1.2, D2.2, D3.1
+3.3VA: BluePill1.40, Header2.1, R1.2, R3.2, R5.2
GND: Alim_5V1.2, BluePill1.19, BluePill1.20, BluePill1.39, C1.2, C2.2, C3.2, Header1.2, Header1.4, Header2.2, Q1.3, Q2.3, Q3.3, Q4.3, SW1.2, SW2.2, SW3.2
unnamed: Alim_5V1.1, D3.2
unnamed: BluePill1.5, Header1.1
unnamed: BluePill1.6, Header1.3
unnamed: BluePill1.7, Header1.12
unnamed: BluePill1.8, Header1.11
unnamed: BluePill1.9, Header1.10
unnamed: BluePill1.10, Header1.9
unnamed: BluePill1.11, Header1.8
unnamed: BluePill1.12, Header1.7
unnamed: BluePill1.15, Header1.6
unnamed: BluePill1.16, Header1.5
unnamed: BluePill1.21, R14.1
unnamed: BluePill1.22, R6.1
unnamed: BluePill1.23, R4.1
unnamed: BluePill1.24, R2.1
unnamed: BluePill1.25, R13.1
unnamed: BluePill1.26, R12.1
unnamed: BluePill1.27, R11.1
unnamed: BluePill1.30, Header2.3
unnamed: BluePill1.31, Header2.4
unnamed: BluePill1.32, Header2.5
unnamed: BluePill1.33, Header2.7
unnamed: BluePill1.34, Header2.6
unnamed: BluePill1.35, Header2.8
unnamed: BluePill1.36, Header2.9
unnamed: BluePill1.37, Header2.10
unnamed: C1.1, R1.1, R2.2, SW1.1
unnamed: C2.1, R3.1, R4.2, SW2.1
unnamed: C3.1, R5.1, R6.2, SW3.1
unnamed: D1.1, R7.1
unnamed: D1.3, R8.1
unnamed: D1.4, R9.1
unnamed: D2.1, R10.1
unnamed: Q1.1, R7.2
unnamed: Q1.2, R11.2
unnamed: Q2.1, R8.2
unnamed: Q2.2, R12.2
unnamed: Q3.1, R9.2
unnamed: Q3.2, R13.2
unnamed: Q4.1, R10.2
unnamed: Q4.2, R14.2

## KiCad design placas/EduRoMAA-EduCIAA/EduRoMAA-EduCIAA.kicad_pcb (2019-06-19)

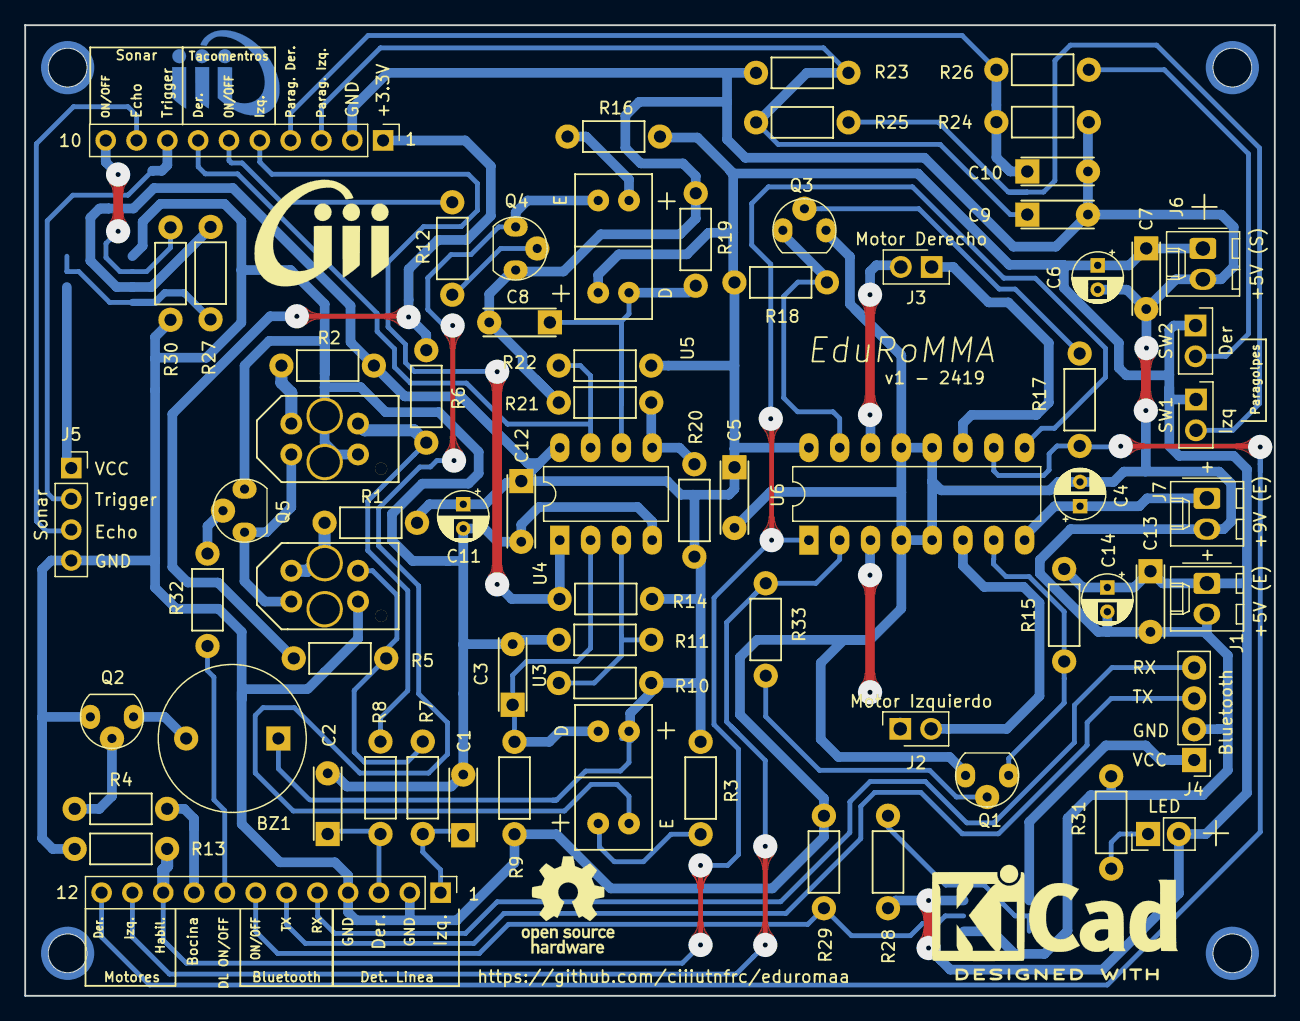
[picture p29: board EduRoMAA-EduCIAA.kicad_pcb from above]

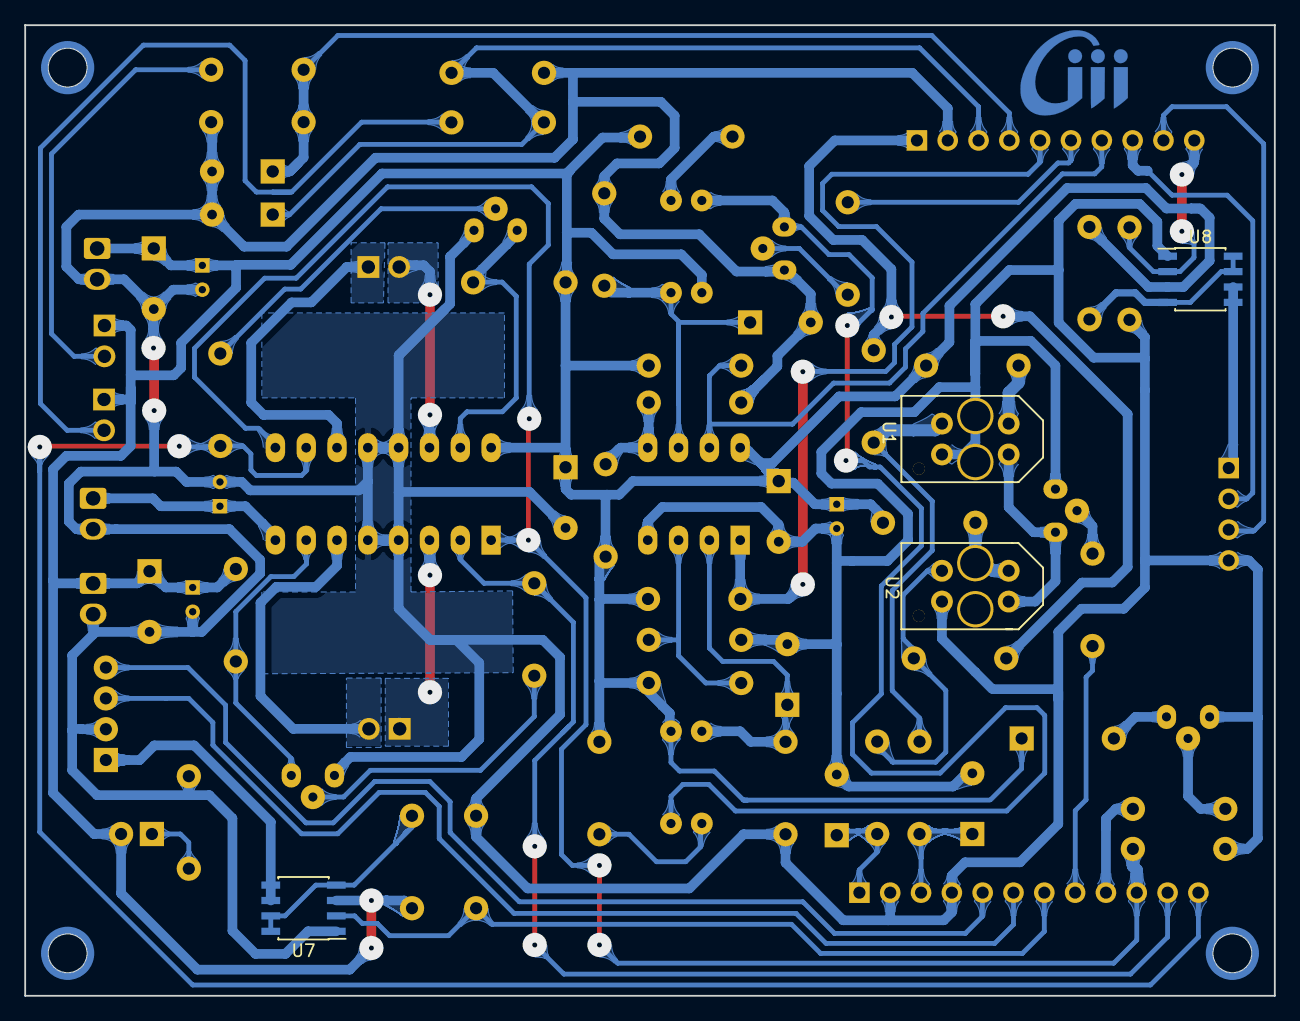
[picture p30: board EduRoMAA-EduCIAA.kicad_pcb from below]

Board: 2 copper layers, 103.0 x 80.0 mm, 81 parts (5 on the bottom side), 53 nets.

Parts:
BZ1: Buzzer; Buzzer_12x9.5RM7.6
C1, C2, C3, C5, C7, C8, C9, C10, C12, C13: 0.1u; C_Disc_D6_P5
C4, C6, C11: 10u; CP_Radial_D4.0mm_P2.00mm
C14: 100u; CP_Radial_D4.0mm_P2.00mm
ConDer1: Conn_01x10; PinHeader_1x10_P2.54mm_Vertical
ConIzq1: Conn_01x12; PinHeader_1x12_P2.54mm_Vertical
D1: LED; PinHeader_1x02_P2.54mm_Vertical
J1, J7: DC_IN; Molex_KK-254_AE-6410-02A_1x02_P2.54mm_Vertical
J2: Motor_Izq; HDRV2W64P254_1X2_508X254X864
J3: Motor_Der; HDRV2W64P254_1X2_508X254X864
J4: Bluetooth; PinHeader_1x04_P2.54mm_Vertical
J5: Sonar; PinSocket_1x04_P2.54mm_Vertical
J6: DC_OUT; Molex_KK-254_AE-6410-02A_1x02_P2.54mm_Vertical
Logo_1: Logo_CIII; Logo_CIII_Small
Logo_2: Logo_CIII; Logo_CIII_Small_FSilk
Logo_3: Logo_ohw; OSHW-Logo_7.5x8mm_SilkScreen
Logo_4: Logo_KiCad; KiCad-Logo2_8mm_SilkScreen
MH1, MH2, MH3, MH4: MountingHole; MountingHole_3.2mm_M3_DIN965
Q1, Q2, Q3, Q4, Q5: BC548; TO-92_mod
R1, R2, R3, R16: 220; Resistor_Horizontal_RM7mm
R4, R12, R17, R31, R32, R33: 1k; Resistor_Horizontal_RM7mm
R5, R6: 3.3k; Resistor_Horizontal_RM7mm
R7, R8, R23, R24: 22k; Resistor_Horizontal_RM7mm
R9, R10, R11, R13, R14, R15, R18, R19, R20, R21, R22, R25, R26, R27, R28, R29, R30: 10k; Resistor_Horizontal_RM7mm
SW1, SW2: SW_Push; HDRV2W64P254_1X2_508X254X864
U1, U2: TCRT5000
U3, U5: TCST1103
U4: LM393; DIP-8_W7.62mm_LongPads
U6: L293D; DIP-16_W7.62mm_LongPads
U7, U8: IRF7105; SOIC-8_3.9x4.9mm_P1.27mm

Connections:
+3V3: ConDer1.1, R5.1, R6.1
+5V: BZ1.1, C5.1, C6.1, C7.1, C11.1, C12.1, C13.1, C14.1, D1.2, J1.1, J6.1, R1.1, R2.1, R3.1, R10.1, R14.1, R15.1, R16.1, R18.1, R20.1, R22.1, R27.1, R28.1, SW1.1, SW2.1, U3.3, U4.8, U5.3, U6.16, U7.3, U8.3
+9V: C4.1, J7.1, U6.8
/C_1: Q1.1, R15.2, U6.7
/C_2: Q3.1, R18.2, U6.15
/Motor_Der1: J3.1, U6.11
/Motor_Der2: J3.2, U6.14
/Motor_Izq1: J2.1, U6.3
/Motor_Izq2: J2.2, U6.6
/Vcc_BT: J4.1, U7.5, U7.6
/Vcc_Sonar: J5.1, U8.5, U8.6
Bluetooth_OnOff: ConIzq1.7, R29.1, U7.2
Bluetooth_Rx: ConIzq1.5, J4.4
Bluetooth_Tx: ConIzq1.6, J4.3
Bumper_Der: C10.1, ConDer1.4, R24.1, R26.1
Bumper_Izq: C9.1, ConDer1.3, R23.2, R25.1
Buzzer: ConIzq1.9, R4.2
ENABLE_Motors: ConIzq1.10, R13.1, U6.1, U6.9
Encoder_Der: ConDer1.7, R22.2, U4.7
Encoder_Izq: ConDer1.5, R14.2, U4.1
Encoder_OnOff: ConDer1.6, R12.2
GND: C1.2, C2.2, C3.2, C4.2, C5.2, C6.2, C7.2, C8.2, C9.2, C10.2, C11.2, C12.2, C13.2, C14.2, ConDer1.2, ConIzq1.2, ConIzq1.4, J1.2, J4.2, J5.4, J6.2, J7.2, Q1.3, Q2.3, Q3.3, Q4.3, Q5.3, R9.2, R11.2, R13.2, R19.2, R21.2, R23.1, R24.2, R29.2, R30.2, R31.1, U1.4, U2.4, U4.4, U6.4, U6.5, U6.12, U6.13, U7.1, U8.1
GND_IRLED1: Q5.1, U1.2, U2.2
GND_LED2: Q4.1, U3.2, U5.2
unnamed: BZ1.2, Q2.1
unnamed: C3.1, R9.1, U3.4, U4.2
unnamed: C8.1, R19.1, U4.6, U5.4
unnamed: D1.1, R31.2
unnamed: Q1.2, R33.1
unnamed: Q2.2, R4.1
unnamed: Q3.2, R17.1
unnamed: Q4.2, R12.1
unnamed: Q5.2, R32.1
unnamed: R1.2, U2.1
unnamed: R2.2, U1.1
unnamed: R3.2, U3.1
unnamed: R5.2, R7.2, U2.3
unnamed: R6.2, R8.2, U1.3
unnamed: R10.2, R11.1, U4.3
unnamed: R16.2, U5.1
unnamed: R20.2, R21.1, U4.5
unnamed: R25.2, SW1.2
unnamed: R26.2, SW2.2
unnamed: R27.2, U8.4, U8.7, U8.8
unnamed: R28.2, U7.4, U7.7, U7.8
PWM_Der: ConIzq1.12, R17.2, U6.10
PWM_Izq: ConIzq1.11, R33.2, U6.2
SegLinea_Der: C2.1, ConIzq1.3, R8.1
SegLinea_Izq: C1.1, ConIzq1.1, R7.1
SegLinea_OnOff: ConIzq1.8, R32.2
Sonar_Echo: ConDer1.9, J5.3
Sonar_OnOff: ConDer1.10, R30.1, U8.2
Sonar_Trig: ConDer1.8, J5.2

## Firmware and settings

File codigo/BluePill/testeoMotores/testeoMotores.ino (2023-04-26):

#define LED_BUILTIN PC13

//Defines de la placa
#define LED_ROJO PB12
#define LEDRGB_ROJO PA10
#define LEDRGB_VERDE PA9
#define LEDRGB_AZUL PA8

#define SW1 PB15
#define SW2 PB14
#define SW3 PB13

//Defines del EDU-RoMAA

#define PARAGOLPE_IZQ PA15
#define PARAGOLPE_DER PB3
#define BOCINA PA5

#define MOTORS_ENABLE PA4
#define MOTOR_IZQ PA3
#define MOTOR_DER PA2

#define INFRAREDS_ENABLE PA6
#define INFRARED_IZQ PA0
#define INFRARED_DER PA1


// the setup function runs once when you press reset or power the board
void setup() {
  // initialize digital pin LED_BUILTIN as an output.
  pinMode(LED_BUILTIN, OUTPUT);
  pinMode(LED_ROJO, OUTPUT);
//  pinMode(LED_ROJO, PWM);
  pinMode(LEDRGB_ROJO, OUTPUT);
  pinMode(LEDRGB_VERDE, OUTPUT);
  pinMode(LEDRGB_AZUL, OUTPUT);
  //pinMode(LEDRGB_AZUL, PWM);
  pinMode(SW1, INPUT);
  pinMode(SW2, INPUT);
  pinMode(SW3, INPUT);

  pinMode(PARAGOLPE_IZQ, INPUT);
  pinMode(PARAGOLPE_DER, INPUT);

  pinMode(BOCINA, OUTPUT);

  pinMode(MOTOR_IZQ, OUTPUT);
  pinMode(MOTOR_DER, OUTPUT);
  pinMode(MOTORS_ENABLE, OUTPUT);

  pinMode(INFRAREDS_ENABLE, OUTPUT);
  pinMode(INFRARED_IZQ, INPUT);
  pinMode(INFRARED_DER, INPUT);
  digitalWrite(MOTORS_ENABLE, HIGH);
}


// the loop function runs over and over again forever
void loop() {
  digitalWrite(LED_BUILTIN, HIGH);   // turn the LED on (HIGH is the voltage level)
  delay(100);                       // wait for a second
  digitalWrite(LED_BUILTIN, LOW);    // turn the LED off by making the voltage LOW
  delay(100);                       // wait for a second

 
 digitalWrite(INFRAREDS_ENABLE, HIGH);
 int INFRARED_IZQ_value = analogRead(INFRARED_IZQ);
 int INFRARED_DER_value = analogRead(INFRARED_DER);
 
 int dutyCycle_ledAzul = map(INFRARED_IZQ_value, 0, 4095, 0, 65535);
 int dutyCycle_ledRojo = map(INFRARED_DER_value, 0, 4095, 0, 65535);
 
 //analogWrite(LEDRGB_AZUL, dutyCycle_ledAzul);
 //analogWrite(LED_ROJO, dutyCycle_ledRojo);

// pwmWrite(LEDRGB_AZUL, dutyCycle_ledAzul);
// pwmWrite(LED_ROJO, dutyCycle_ledRojo);

int velocidad = 0;
for (velocidad =0; velocidad <= 65535; velocidad++){
   analogWrite(MOTOR_IZQ, velocidad);
   analogWrite(MOTOR_DER, velocidad);
   delay(50);
}
   //analogWrite(MOTOR_IZQ, dutyCycle_ledAzul);
   //analogWrite(MOTOR_DER, dutyCycle_ledRojo);
}

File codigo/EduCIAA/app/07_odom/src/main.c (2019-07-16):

/*
 * main.c
 *
 *  Created on: 14 jul. 2019
 *      Author: marti
 */

/*==================[inclusiones]============================================*/

#include "eduromaa.h"

/*==================[definiciones]===========================================*/

#define MARCHA_NORMAL 70
#define MARCHA_LENTA  50
#define MOTOR_PARADO  0

#define DIAMETRO_RUEDAS_CM   6.67   // Diámetro de las ruedas [cm]
#define RANURAS_ENCODER     20      // Cantidad de ranuras del encoder
// Longitud del arco de la rueda entre 2 pulsos de enconder
#define DIST_CUENTA_CM (3.1416 * DIAMETRO_RUEDAS_CM / RANURAS_ENCODER)

uint8_t procesar_sonar(void);
void procesar_seguidor_linea(uint8_t vel_ruedas);

/*==================[implementaciones]=======================================*/
int main(void)
{

    uint32_t ti_cuenta_anterior, ti_dist_recorrida, ti_rpm;
    uint8_t td_vel_cuentas_seg, td_vel_cm_seg;
    uint32_t td_cuenta_anterior, td_dist_recorrida, td_rpm;
    uint8_t ti_vel_cuentas_seg, ti_vel_cm_seg;

    uint8_t marcha;

    // Variables para Retardos NO bloqueantes
    delay_t retardo_ir, retardo_uart, retardo_odometria;
    tacometro_t tacoIzq, tacoDer;

    iniEduromaa();  // Inicializa EduRoMAA

    /* Prender solo los Módulos a utilizar */
    prenderSensoresIR();
    prenderSonar();
    prenderMotores();
    prenderTacometros();

    marcha = 0;
    ti_dist_recorrida = 0;
    delayInit(&retardo_ir, 20);
    delayInit(&retardo_odometria, 1000);
    delayInit(&retardo_uart, 2000);


    while (1)
    {
        if (delayRead(&retardo_ir))
        {
            marcha = procesar_sonar();
            procesar_seguidor_linea(marcha);
        }

        if (delayRead(&retardo_odometria))
        {
            leerTacometros(&tacoIzq, &tacoDer);

            ti_vel_cuentas_seg = tacoIzq.cuenta - ti_cuenta_anterior;
            ti_vel_cm_seg = ti_vel_cuentas_seg * DIST_CUENTA_CM;
            ti_rpm = ti_vel_cuentas_seg * 3;// <--¿De dónde sale el 3?
            ti_dist_recorrida += ti_vel_cm_seg;
            ti_cuenta_anterior = tacoIzq.cuenta;

            td_vel_cuentas_seg = tacoDer.cuenta - td_cuenta_anterior;
            td_vel_cm_seg = td_vel_cuentas_seg * DIST_CUENTA_CM;
            td_rpm = td_vel_cuentas_seg * 3;// <--¿De dónde sale el 3?
            td_dist_recorrida += td_vel_cm_seg;
            td_cuenta_anterior = tacoDer.cuenta;

        }

        if (delayRead(&retardo_uart))
        {

            printf("Ti[c/s]: %d\tTi[cm/s]: %d\tTi[rpm]:%d\tTi[cm]:%d\r\n",
                    ti_vel_cuentas_seg, ti_vel_cm_seg, ti_rpm,
                    ti_dist_recorrida);
            printf("Td[c/s]: %d\tTd[cm/s]: %d\tTd[rpm]:%d\tTd[cm]:%d\r\n",
                                td_vel_cuentas_seg, td_vel_cm_seg, td_rpm,
                                td_dist_recorrida);
        }
    }

    /* NO DEBE LLEGAR NUNCA AQUI, ¿el programa se ejecuta eternamente? */
    return 0;
}

uint8_t procesar_sonar(void)
{
    float dist_cm;

    leerSonar(&dist_cm);

    if (dist_cm < 5)
    {
        return MOTOR_PARADO;
    } else if (dist_cm < 10)
    {
        return MARCHA_LENTA;

    } else
    {
        return MARCHA_NORMAL;
    }
}

void procesar_seguidor_linea(uint8_t vel_ruedas)
{
    switch (seguir_linea())
    {
    case LINEA_IZQ_DER_OK:
        gpioWrite(LED1, OFF);
        gpioWrite(LED2, ON);
        gpioWrite(LED3, OFF);
        /* Motores: ambos avanzan a la misma velocidad */
        escribirMotores(vel_ruedas, vel_ruedas);
        break;
    case LINEA_DER_OK:
        gpioWrite(LED1, ON);
        gpioWrite(LED2, OFF);
        gpioWrite(LED3, OFF);
        /* Motores: motor izquierdo avanza a mayor velocidad que el derecho */
        escribirMotores(vel_ruedas/2, vel_ruedas);
        break;
    case LINEA_IZQ_OK:
        gpioWrite(LED1, OFF);
        gpioWrite(LED2, OFF);
        gpioWrite(LED3, ON);
        /* Motores: motor derecho avanza a mayor velocidad que el izquierdo */
        escribirMotores(vel_ruedas, vel_ruedas/ 2);
        break;
    case LINEA_DETENER:
    default:
        gpioWrite(LED1, OFF);
        gpioWrite(LED2, OFF);
        gpioWrite(LED3, OFF);
        /* Motores: ambos motores se detienen */
        escribirMotores(MOTOR_PARADO, MOTOR_PARADO);
        break;
    }
}

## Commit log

2019-04-26 Agregado archivos de CAD 3D
    [EduRoMAAAtras.fcstd, EduRoMAAFrente.fcstd, EduRoMAALaterales.fcstd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]
2019-04-29 Editado archivo FreeCAD de las tapas del robot
    Eliminado un hueco de sujeción con tornillos, queda uno solo.
    Agregado archivo .gitignore para ignorar archivos backups de FreeCAD.
    [EduRoMAATapas.fcstd]
2019-05-04 Editado diseño CAD de las tapas superior e inferior
    Corregido error de cotas de referencia de la tapa superior.
    [EduRoMAATapas.fcstd]
2019-05-04 Perforaciones de tapa superior
    Agregada perforaciones para sujetar la placa EduCIAA a la tapa superior
    [EduRoMAATapas.fcstd]
2019-05-04 Editado CAD de la tapa inferior
    Agregado perforaciones para los tornillos de sujeción de la placa de
    acondicionamiento a la tapa inferior
    [EduRoMAATapas.fcstd]
2019-05-06 Modificado diseño 3D de la tapa inferior
    Modificado para coincidir con las dimensiones del PCB.
    [EduRoMAATapas.fcstd]
2019-05-06 Modificado diseño 3D de tapa superior
    Modificada ranura pasacables y huecos para los tornillos de la EduCIAA
    de la tapa superior.
    [EduRoMAATapas.fcstd]
2019-05-06 Corregido error de encastres en tapa superior
    [EduRoMAATapas.fcstd]
2019-05-07 Firmware EduROMAA: primera versión funcional
    Archivo Readme.md contiene todas las definiciones del pinout de la placa
    EduCIAA para conexión con EduRoMAA.
    * Módulo Paragolpes:
    * En "paragolpes.h" se encuentran 2 implementaciones:
    * Utilizando solo GPIO para leer el estado de cada paragolpes
    * Utilizando interrupciones externas
    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
2019-05-11 Corregido error de guardabarros
    Corregido error de 5mm en los guardabarros, se corrieron los laterales
    hacia adentro.
    [EduRoMAATapas.fcstd]
2019-05-11 Archivos para generar el dibujo para el PCB
    Agregados archivos que permiten generar el dibuo (en formato dxf) de
    ayuda para ubicar los componentes de la placa (PCB).
    [DibujoPCB.dxf, DibujoPCB.fcstd]
2019-05-16 Corregido error del diseño CAD de los laterales
    Corregido error en el diseño CAD de los encastres de los motores en los
    laterales del robot.
    [EduRoMAALaterales.fcstd]
2019-05-20 Agregado archivo de ensamble de la estructura
    Agregado archivo de ensamble de la estructura del robot, el cual incluye
    las tapas inferior y superior, los laterales, la tapa delantera y
    trasera.
    [EsambleEstructura.fcstd]
2019-05-20 Agregado archivos para el corte láser (svg y pdf)
    Modificado los archivos de diseño para agregar proyección 2D para
    exportar a svg.
    Creado archivos svg para corte láser y pdf con todas las piezas.
    [EduRoMAAFrente.fcstd, EduRoMAALaterales.fcstd, EduRoMAATapas.fcstd]
2019-05-20 Modificado archivo de ensample de estructura
    Actualizada tapa inferior con versión con perforaciones de la placa de
    acondicionamiento.
    [EsambleEstructura.fcstd]
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2019-05-21 Agregado diseño de pieza de apoyo
    Agregado diseño de pieza de apoyo que hace de reemplazo de una rueda
    castor.
    Agregado transparencia a las piezas del ensamble.
    [EduRoMAACastor.fcstd, EduRoMAACastor.stl, EsambleEstructura.fcstd]
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2019-05-30 Modificada diseño CAD 3D de la tapa superior
    Tapa superior modificada para incluir las perforaciones para la carga de
    la baterías. Modificados también los archivos de corte (.svg)
    [EduRoMAATapas.fcstd]
2019-05-30 Modificado archivo README.md de la raíz
    Agregado enlace a video de YouTube en README raíz.
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2019-05-31 [placas] Agregando la placa EduRoMAA-EduCIAA al proyecto
    [Base.dxf, Buzzer.iges, Buzzer.step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]
2019-06-03 Módulo Bluetooth y mejoras varias
    * Agregado módulo Bluetooth y programado prueba de uso. La prueba
    devuelve por el puerto USB lo recibido por BT.
    * Mofificado iniMotores para que devuelva "void" ya que no tiene
    condición de bloqueo.
    * Modificado código de prueba de motores para que genere rampas de
    velocidad en avance y en retroceso.
    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
2019-06-03 Reorganizo esquematico y uno librerias
    Reorganización general, elimino net repetidas y uno las librerias en una sola
    [EduRoMAA-EduCIAA.sch]
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2019-06-10 [PCB] Modifico serigrafia y re-ruteo.
    Modifico serigrafia y algo de ruteo
    [EduRoMAA-EduCIAA.kicad_pcb, EduRoMAA-EduCIAA.sch]
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2019-06-11 [PCB] Revisiones de ruteado.
    [EduRoMAA-EduCIAA.kicad_pcb]
2019-06-13 [PCB] Agrego serigrafia complementaria
    Agrego símbolos para serigrafia, lista para revision
    [EduRoMAA-EduCIAA.kicad_pcb, EduRoMAA-EduCIAA.sch]
2019-06-13 [PCB] Arreglo teardrops
    [EduRoMAA-EduCIAA.kicad_pcb, EduRoMAA-EduCIAA.sch]
2019-06-13 [PCB] Minimas modificaciones al ruteo, falta hacer un DRC
    [EduRoMAA-EduCIAA.kicad_pcb]
2019-06-14 [PCB] Agrego nombre de placa y reorganizo pistas.
    [EduRoMAA-EduCIAA.kicad_pcb]
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2019-06-15 Renombrado de directorios
    [Base.dxf, Buzzer.iges, Buzzer.step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]
2019-06-18 Agrego BOM, PDF y modifico esquematico
    Se modifica las resistencias R5,R6 a 3,3kohm. Se modifica fp
    de uno de los TCRT5000, agrego pdf de serigrafia frontal,
    pistas inferiores y archivos para fabricacion.
    Agrego BOM, interactivo y html.
    [EduRoMAA-EduCIAA.kicad_pcb, EduRoMAA-EduCIAA.sch]
2019-06-19 Actualizo footprints y modifico pdf de fabricacion
    Se dibujo la capa de fabricacion en el footprints de los componentes,
    se agrego contorno, puentes, en capa de fabricacion, exporto todo en
    pdf Ffab.
    [EduRoMAA-EduCIAA.kicad_pcb]
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2023-03-17 [EduRoMAA-BluePill] Agrega archivos kicad Agrega los archivos kicad del pcb de la placa de adaptacion
    [BluePillAcond.kicad_pcb, BluePillAcond.sch]
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
